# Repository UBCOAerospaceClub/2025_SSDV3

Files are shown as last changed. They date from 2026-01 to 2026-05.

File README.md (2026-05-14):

# The Super Step Down V3

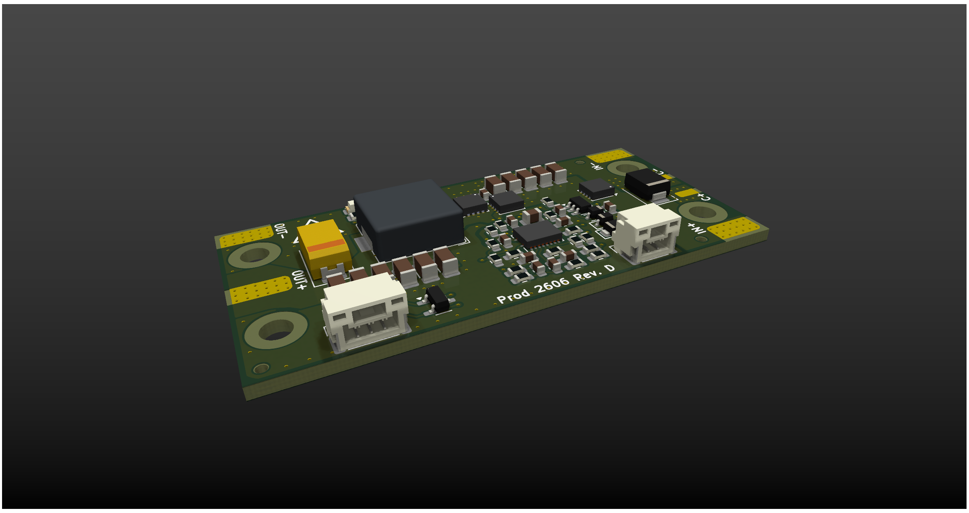
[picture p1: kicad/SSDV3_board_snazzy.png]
Top View


The SSDV3 is an independently-made, non-isolated DC/DC converter designed for unmanned aerial systems (UAS). The module is intended for converting 50V battery input down to 5-12V output at a maximum load of 8A. It acts as a reliable battery-eliminator circuit (BEC) through effective regulation in the presence of large line voltage and load current transients.

## Comparison with Last Super Step Down

This design is motivated by the challenges encountered by the [UBCO Aerospace Club](https://github.com/UBCOAerospaceClub) with their Jellyfish quadcopter when powering auxiliary electronics off the drone's main battery. Lessons were learned through a variety of integration failures, investigations, and verification, and these experiences informed the development of version 3 of the Super Step Down series.

Comparison

**Improvements from the previous version:**

- Dramatically improved regulation during line and load transients
- Considerable footprint area reduction by 16.5%
- Configurable output voltages instead of a fixed 5V output
- Added ESD protection on inputs
- Features reverse polarity protection
- Uses direct solder pads instead of terminal block for output connection

## Documentation

[Super Step Down V3 Documentation](https://docs.google.com/document/d/1HDTwUbcQu91JqGZ-epUO-CT9nVxvoZJ6mtjSmItczHE/edit?usp=sharing)

## Specifications

<table><tbody>
  <tr>
    <td>Input Voltage</td>
    <td>20-60V</td>
  </tr>
  <tr>
    <td>Max Transient Voltage</td>
    <td>100V (clamping starts at 70V)</td>
  </tr>
  <tr>
    <td>Output Voltage(s)</td>
    <td>5.1V, 7.4V, 12V</td>
  </tr>
  <tr>
    <td>Max Output Current*</td>
    <td>8A</td>
  </tr>
  <tr>
    <td>Typical Efficiency</td>
    <td>88%</td>
  </tr>
  <tr>
    <td>Voltage Transient Deviation</td>
    <td>±2.5%</td>
  </tr>
</tbody>
</table>

### Performance Curves

**Voltage ripple at 5.1V Output**

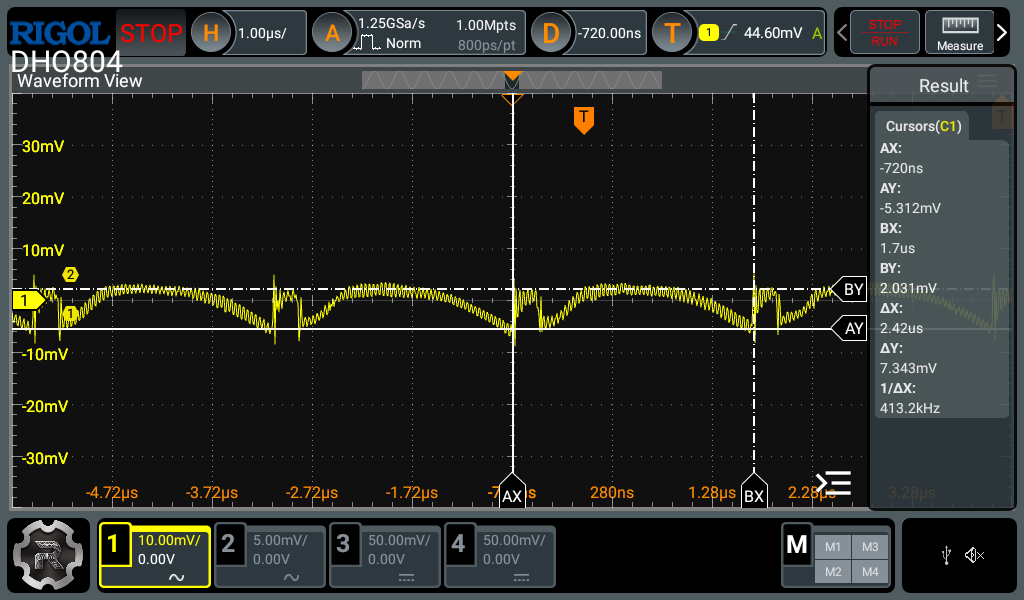
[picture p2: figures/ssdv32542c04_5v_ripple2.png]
Voltage ripple 5.1V


**Transient response of 5.1V 5-0A Output**

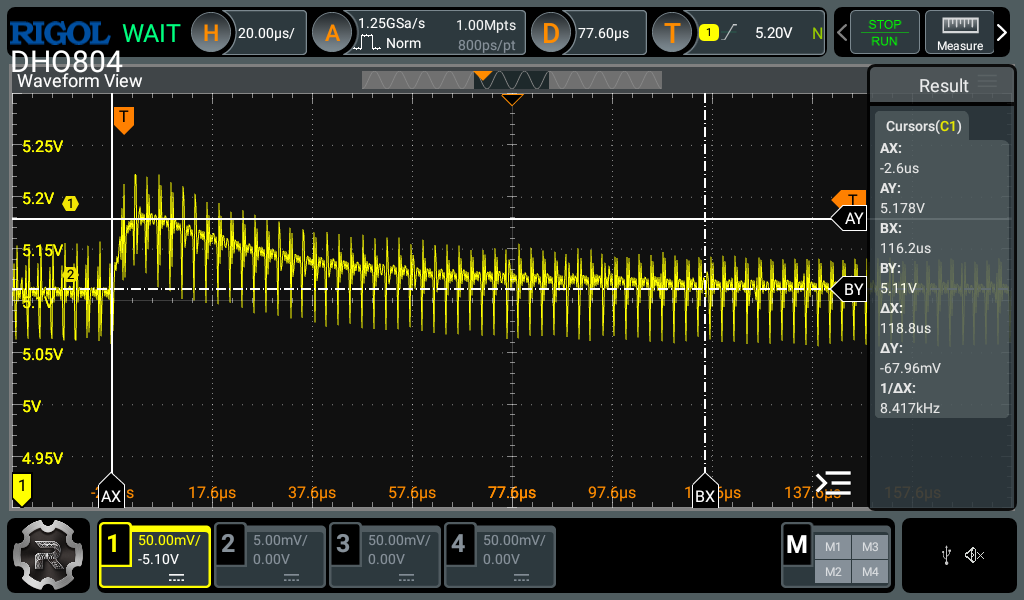
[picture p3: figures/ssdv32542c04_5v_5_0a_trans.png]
Transient response


**Efficiency Measurements, 50-V Input**

Efficiency curves

## Copyright Notice

Copyright &#169; Julian Joaquin 2026

Documentation and media are licensed under CC BY-SA 4.0

Hardware Source Licensed under CERN-OHL-W version 2

UBCO is registered trademark of the University of British Columbia. The use of UBC trademarks in this project are only for identification, and do not indicate association or endorsement. For guidelines on the permitted uses of UBC trademarks, please see http://universitycounsel.ubc.ca/university-trade-marks/.

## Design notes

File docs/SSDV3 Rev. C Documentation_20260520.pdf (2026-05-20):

### Super Step Down Documentation – SSDV3 Rev. C

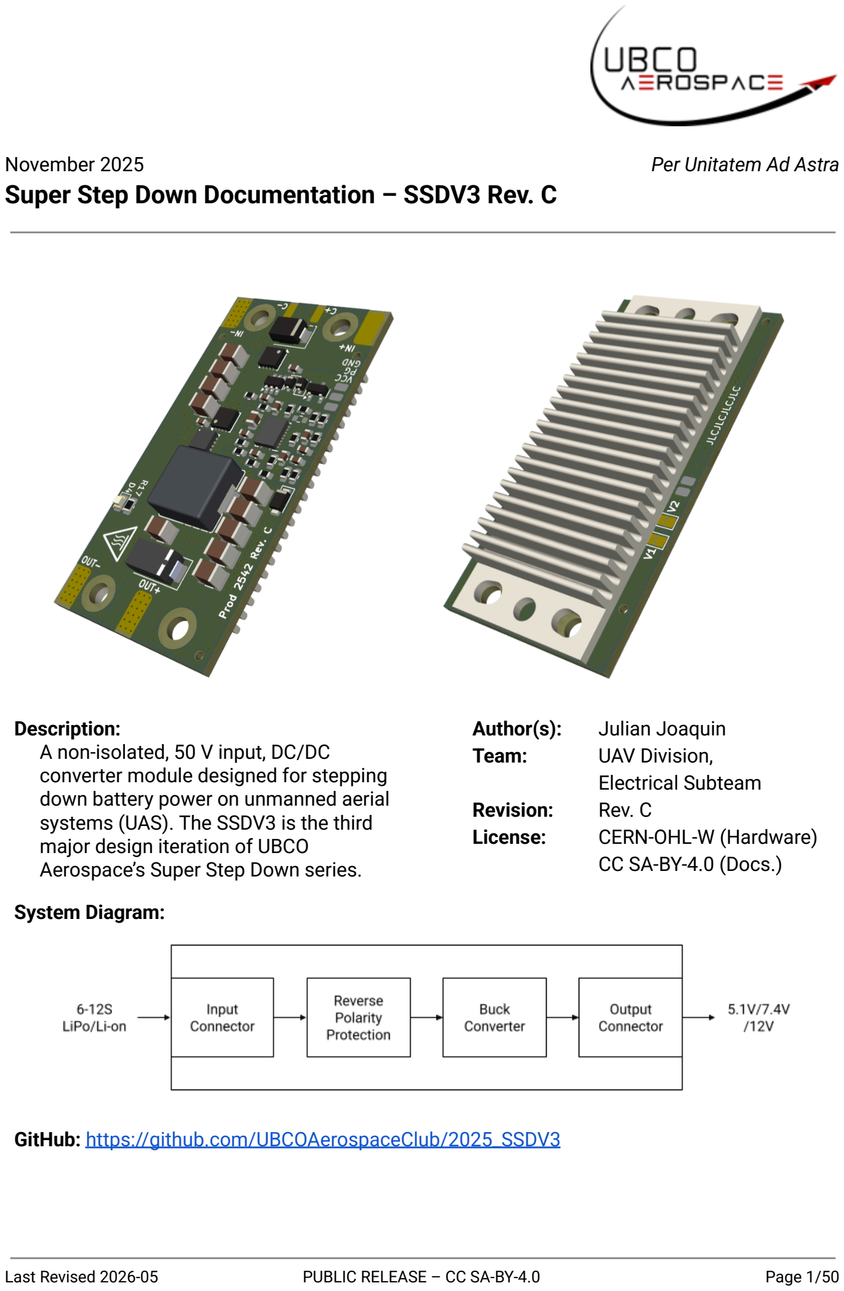
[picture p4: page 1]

November 2025 | Per Unitatem Ad Astra

Description:
A non-isolated, 50 V input, DC/DC converter module designed for stepping down battery power on unmanned aerial systems (UAS). The SSDV3 is the third major design iteration of UBCO Aerospace’s Super Step Down series.
Author(s): | Julian Joaquin
Team: | UAV Division,
| Electrical Subteam
Revision: | Rev. C
License: | CERN-OHL-W (Hardware)
| CC SA-BY-4.0 (Docs.)

System Diagram:

GitHub: https://github.com/UBCOAerospaceClub/2025_SSDV3

Last Revised 2026-05 | PUBLIC RELEASE – CC SA-BY-4.0 | Page 1/50

SSDV3 Rev. C Documentation

### Important Notice

The Complete Source material, including technical data, design resources, and other material associated with the SSDV3 project are provided “AS IS” without any guarantee of quality or compliance for commercial use.

UBCO Aerospace holds no rights to the patent of the SSDV3 project or its derivatives. The public documentation through UBCO Aerospace is solely provided for the purpose of compliance with CERN-OHL-W while it adopts the SSDV3 project for its own use.

UBCO is a registered trademark of the University of British Columbia. The use of UBC trademarks in this project are only for identification, and do not indicate association or endorsement from the university. For guidelines on the permitted uses of UBC trademarks, please see http://universitycounsel.ubc.ca/university-trade-marks/.

### Safety Precautions

Warning:
This device is intended to be directly connected to LiPo/Li-ion batteries which, under short-circuit conditions or unsafe handling, have the potential to cause fire or explosion. Take necessary precautions to insulate the device inputs and mitigate the risk of a short circuit.

Caution:
This device becomes hot under normal operation. Wait at least two minutes after powering off and allow the device to cool down to suitable temperatures before handling. When servicing, do not use low melting-point solder alloys, such as those that contain bismuth or indium.

Caution:
The input voltage to this device can be in excess of 60 VDC. Keep conductive materials away from the exposed device inputs. The device must be powered down before it can be handled or serviced.

Caution:
This device is susceptible to damage from electrostatic discharge (ESD). At minimum, refrain from touching any exposed copper or attached components to the PCB when handling without precautionary ESD measures.
Page 2/50 | PUBLIC RELEASE – CC SA-BY-4.0 | Last Revised 2026-05

### Design Revisions

Rev. | Date | Description
A-1 | 2025-07 | Concept design using the LM70880 buck converter and LM5069-1 hot-swap controller. Abandoned due to supply chain issues and cost constraints.
A-2 | 2025-08 | Concept design using the LM5146 buck controller and TPS2490 hot-swap controller. Abandoned due to space and cost constraints.
A-3 | 2025-09 | Concept design using the LM5146 buck controller in a custom 1/8th brick form factor. Accepted design for revision.
B | 2025-10 | Concept design using the cheapest parts available on LCSC. Limited part availability and NRND parts made future production of this revision difficult.
C | 2025-10 | Prototype design featuring reverse polarity protection in exchange for a smaller TVS diode on the input. Smaller, active-production 3x3mm PQFN-8 FETs used in place of SO-8 FETs. Used for preliminary integration testing and verification.
Last Revised 2026-05 | PUBLIC RELEASE – CC SA-BY-4.0 | Page 3/50

### Table of Contents

Page 4/50 | PUBLIC RELEASE – CC SA-BY-4.0 | Last Revised 2026-05

Last Revised 2026-05 | PUBLIC RELEASE – CC SA-BY-4.0 | Page 5/50

### 1 Specifications

### 1.1 Maximum Ratings

Under typical ambient temperature of TA = 21 °C, unless noted otherwise.
Parameter | Min Max | Unit
VIN | Input voltage from VIN+ to VIN- and C+ to C-1 | –60 60 | V
| Maximum transient input voltage 1 | –70 70
IIN | DC Input current | 6 | A
VEN | Input voltage from EN to GND 1 | –60 60 | V
VOUT | Output voltage from VOUT+ to VOUT- | 0 20 | V
IOUT | DC Output current | 8 | A
POUT | Output power for 60 seconds | 100 | W
| Continuous output power with heatsink | 60
| Continuous output power without heatsink | 40
VCC | Output voltage from VCC to GND | 0 7.8 | V
IVCC | Output current from VCC | 0.02 | A
VPG | Output voltage from PG to GND | 0 7.8 | V
TA | Operating ambient temperature range | 0 55 | °C
TSTG | Storage temperature range | 0 85 | °C
1. The input electrolytic capacitor is not protected from reverse polarity.
Page 6/50 | PUBLIC RELEASE – CC SA-BY-4.0 | Last Revised 2026-05

IMPORTANT:
Because of constrained budget, limited time availability, and project urgency, no SSDV3 Rev. C units have been used to verify the absolute maximum ratings. The provided ratings are estimated from available testing data and are not guaranteed to be the absolute maximum ratings before destruction of damage of the module.

### 1.2 Recommended Operating Conditions

Under typical ambient temperature of TA = 21 °C, unless noted otherwise.
Parameter | Min Max | Unit
S | Input LiPo/Li-ion cells in series | 6 12 | cells
VIN | Input voltage | 20 60 | V
| Maximum transient input voltage | 70
IOUT | VIN = 50 V, VOUT = 5.1 V, with heatsink 2 | 8.0 | A
| VIN = 50 V, VOUT = 7.4 V, with heatsink 2 | 5.8
| VIN = 50 V, VOUT = 12.0 V, with heatsink 2 | 4.0
| VIN = 25 V, VOUT = 5.1 V, with heatsink 2 | 8.0
| VIN = 25 V, VOUT = 7.4 V, with heatsink 2 | 8.0
| VIN = 25 V, VOUT = 12.0 V, with heatsink 2 | 6.6
2. Calculated from temperatures of load sweep test.

### 1.3 Electrical Characteristics

Under typical ambient temperature of TA = 21 °C, unless noted otherwise.
Parameter | Test Conditions | Min | Typ. | Max | Unit

### 1.3.1 Input Characteristics

VIN | Input voltage operating range | | 20 50 60 | V
IQ,ON | Quiescent input current, no load | VIN = 50 V, VOUT = 5.1V, no attached load to VOUT | 50 70 | mA
IQ,OFF | Quiescent input current, UVLO | VIN = 10 V | 2.7 | mA

### 1.3.2 Dynamic Characteristics

fSW | Switching frequency | | 417 | kHz
tSS | Soft-start time | VIN = 50 V | 3.6 | ms
IIN,MIN | Minimum startup supply current | VIN = 50 V, VOUT = 12.0 V | 0.6 | A
ΔVMAX | Maximum transient output deviation | VIN = 50 V, VOUT = 5.1V, 5 A load step | ±1.5 ±3.1 | %
Last Revised 2026-05 | PUBLIC RELEASE – CC SA-BY-4.0 | Page 7/50

### 1.3 Electrical Characteristics (continued)

Under typical ambient temperature of TA = 21 °C, unless noted otherwise.
Parameter | Test Conditions | Min | Typ. | Max | Unit

### 1.3.3 Output Characteristics

η | Efficiency | VIN = 50 V, VOUT = 5.1 V, IOUT = 4.3 A | 85 | %
| | VIN = 50 V, VOUT = 7.4 V, IOUT = 2.7 A | 87
| | VIN = 50 V, VOUT = 12.0 V, IOUT = 3.3 A | 91
ΔVPP | Peak-to-peak output voltage ripple | VIN = 50 V, VOUT = 5.1 V | 8.8 15.0 | mVPP
| | VIN = 50 V, VOUT = 7.4 V | 12.3 19.0
| | VIN = 50 V, VOUT = 12.0 V | 27.3 35.0
| | VIN = 25 V, VOUT = 5.1 V | 4.8
| | VIN = 25 V, VOUT = 7.4 V | 7.9
| | VIN = 25 V, VOUT = 12.0 V | 22.1

### 1.3.4 Protection Features

IOCP | OCP current limit threshold 3 | VIN = 50 V, VOUT = 5.1 V | 10.2 | A
| | VIN = 50 V, VOUT = 7.4 V | 10.5
| | VIN = 50 V, VOUT = 12.0 V | 11.6
OCP | Overcurrent protection | VIN = 50 V, VOUT = 5.1 V | PASS | : )
RPP | Reverse polarity protection | VIN = 50 V | FAIL 1 | : (

### 1.3.5 Auxiliary IO Characteristics

VEN,ON | Enable voltage | Input voltage rising | 16.3 | V
VEN,OFF | Undervoltage lockout threshold | Input voltage falling | 14.8 | V
VVCC | VCC nominal voltage | VIN = 50 V | 7.5 | V
VPG | PG nominal voltage | VIN = 50 V | 7.5 | V
1. The input electrolytic capacitor is not protected from reverse polarity.
3. Defined by design, not subject to testing.
Page 8/50 | PUBLIC RELEASE – CC SA-BY-4.0 | Last Revised 2026-05

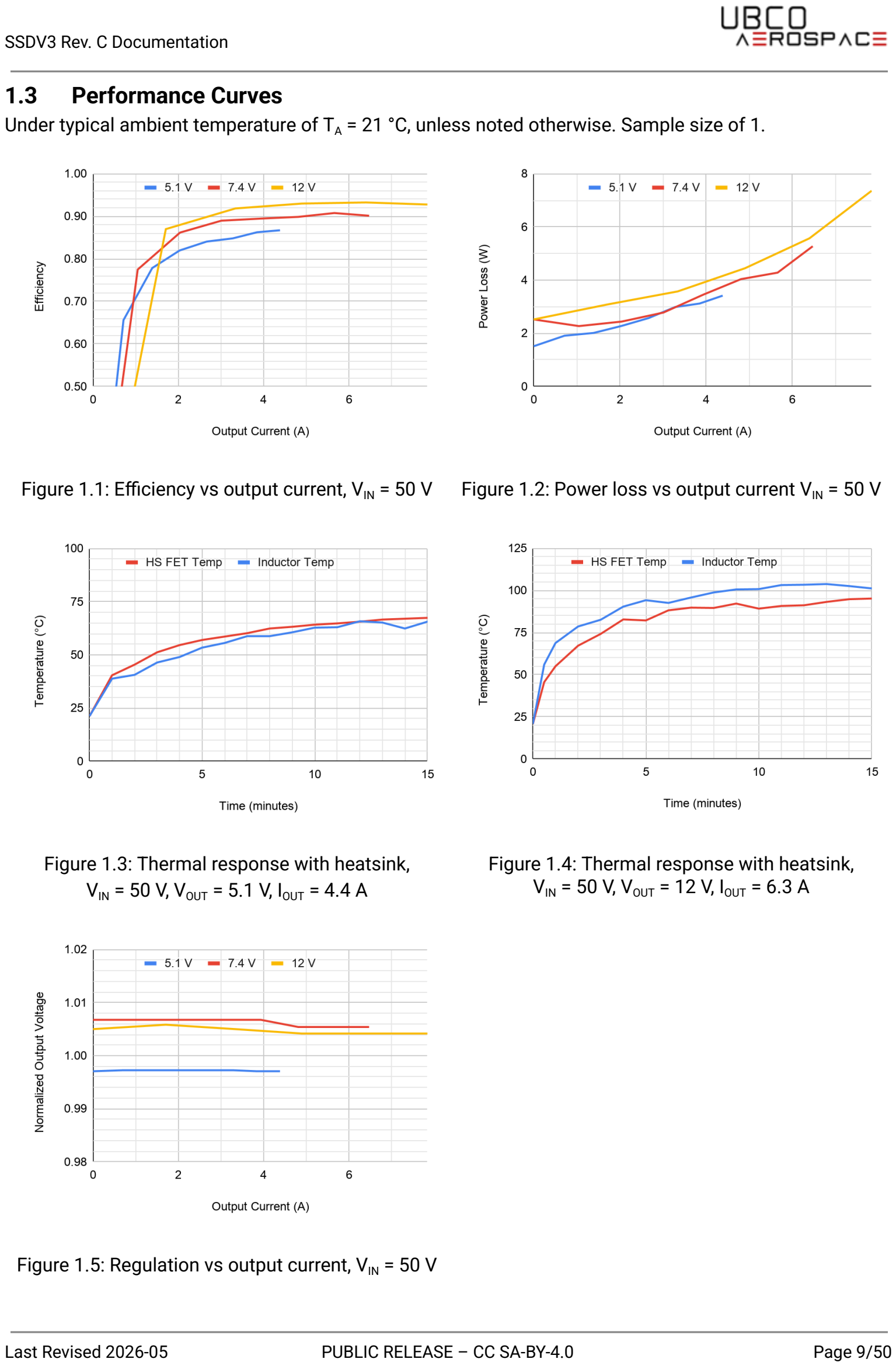
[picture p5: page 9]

### 1.3 Performance Curves

Under typical ambient temperature of TA = 21 °C, unless noted otherwise. Sample size of 1.

Figure 1.1: Efficiency vs output current, VIN = 50 V Figure 1.2: Power loss vs output current VIN = 50 V

Figure 1.3: Thermal response with heatsink, VIN = 50 V, VOUT = 5.1 V, IOUT = 4.4 A

Figure 1.4: Thermal response with heatsink, VIN = 50 V, VOUT = 12 V, IOUT = 6.3 A

Figure 1.5: Regulation vs output current, VIN = 50 V

Last Revised 2026-05 | PUBLIC RELEASE – CC SA-BY-4.0 | Page 9/50

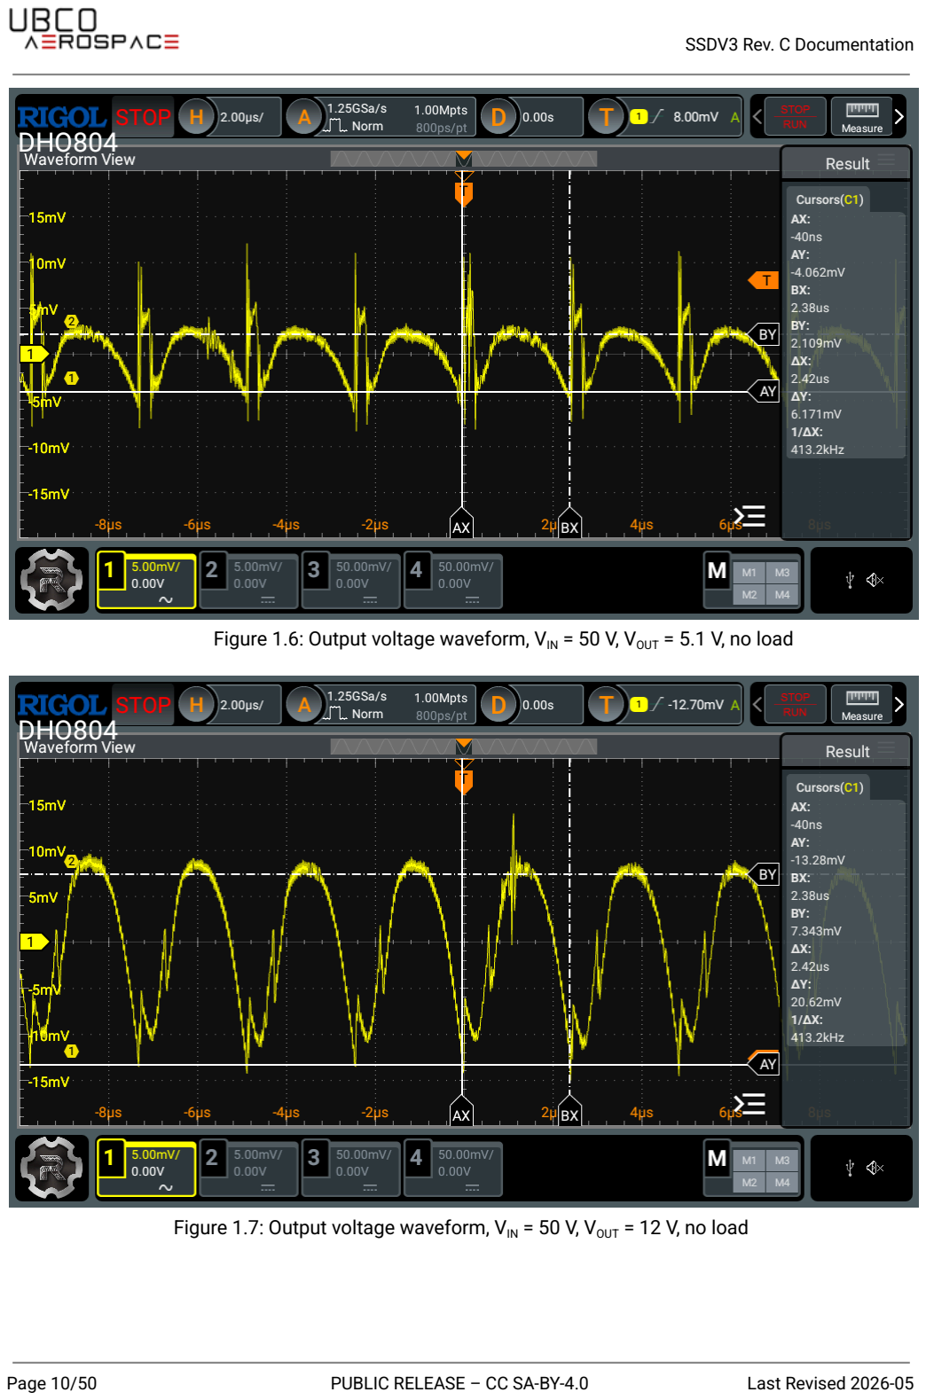
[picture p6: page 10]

Figure 1.6: Output voltage waveform, VIN = 50 V, VOUT = 5.1 V, no load

Figure 1.7: Output voltage waveform, VIN = 50 V, VOUT = 12 V, no load

Page 10/50 | PUBLIC RELEASE – CC SA-BY-4.0 | Last Revised 2026-05

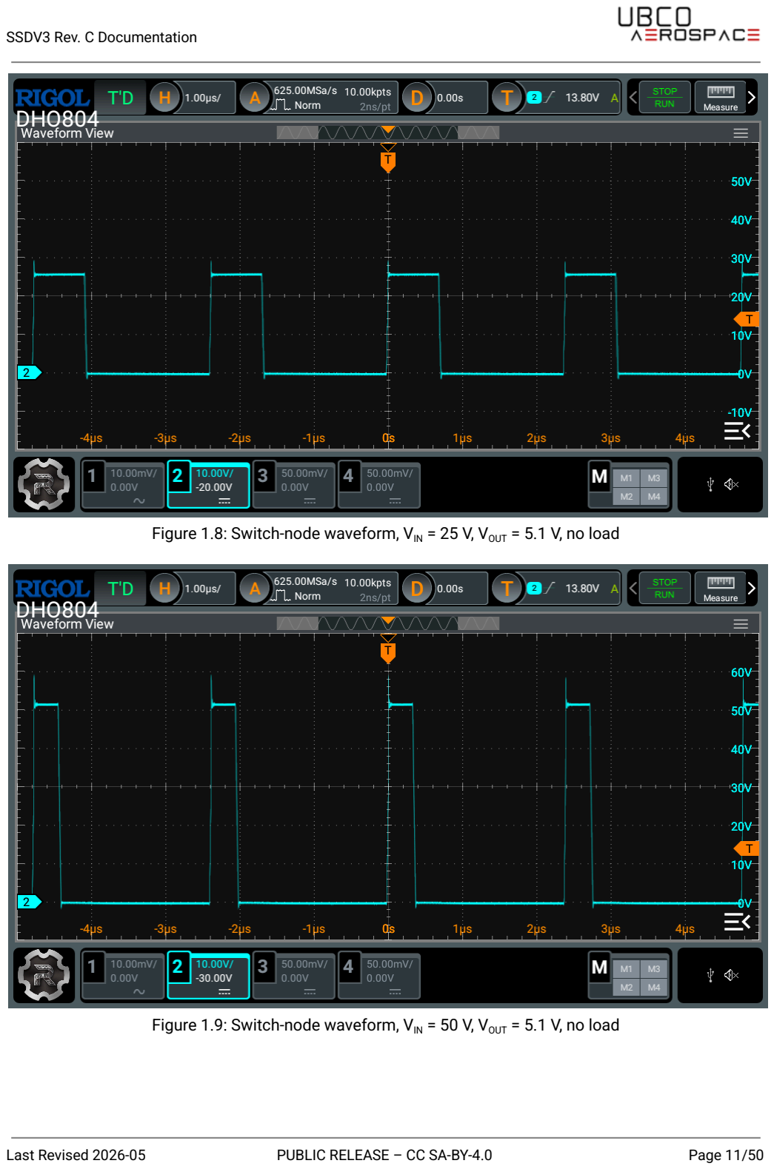
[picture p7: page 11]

Figure 1.8: Switch-node waveform, VIN = 25 V, VOUT = 5.1 V, no load

Figure 1.9: Switch-node waveform, VIN = 50 V, VOUT = 5.1 V, no load

Last Revised 2026-05 | PUBLIC RELEASE – CC SA-BY-4.0 | Page 11/50

Figure 1.10: Output load-on transient, VIN = 50 V, VOUT = 5.1 V, IOUT = 5 A

Figure 1.11: Output load-off transient, VIN = 50 V, VOUT = 5.1 V, IOUT = 5 A

Page 12/50 | PUBLIC RELEASE – CC SA-BY-4.0 | Last Revised 2026-05

### 2 Usage

Please read the Safety Precautions before continuing.

### 2.1 Functional Description

The SSDV3 is a non-isolated, wide input voltage step-down module intended to provide a reliable voltage source for electrically demanding systems requiring power from LiPo/Li-ion batteries. The design offers excellent disturbance rejection from battery voltage sag and sudden load spikes, giving much better performance than other hobbyist devices, making it a strong alternative to commercially-available battery eliminator circuits (BECs) while maintaining a small form-factor. Its extremely robust output regulation makes the SSDV3 best suited for supplying low-voltage devices, especially high-performance embedded computers or sensitive electronics that specify strict 5 V power requirements.

What makes the SSDV3 unique from other market BECs is its design for reliability. The step-down circuitry is protected by a TVS diode to address potential ESD on the battery lines. Copper traces leading from the input pads are designed significantly above specification to mitigate damage from inrush current whenever the battery is plugged in. Additionally, an N-channel MOSFET at the input acts as an ideal diode to protect the module and downstream electronics from a reversed battery connection, at minimal cost to the step-down’s efficiency.

### 2.2 Known Issues

Issue | Severity | Impact | Workaround | Planned Fix
Solder pads expose high-voltage contacts | High | Catastrophic battery short | Kapton tape covering | Board-mount connectors
Electrolytic cap. unprotected from reverse polarity | High | Reverse polarity will explode cap. | Do not reverse input | Reroute cap. to protected net
Thermal output limits current output below 8 A | Medium | Requires heatsink and thermal derating | Limit output | Lower losses
Output cap. placement causes large ESL spikes | Low | Output ripple spikes | None | Improve cap. layout

Table 2.1: Known issue risk assessment.

Last Revised 2026-05 | PUBLIC RELEASE – CC SA-BY-4.0 | Page 13/50

### 2.3 Interfaces

Figure 2.1: Module top interfaces.

Figure 2.2: Module bottom interfaces.

Page 14/50 | PUBLIC RELEASE – CC SA-BY-4.0 | Last Revised 2026-05

### 2.4 Installation Guidelines

- Ensure wires of at least 18 AWG have been soldered onto the input power and output power pads before installing the module. Use power connectors rated for the intended output current, for example the Amass XT30 or Molex Mini-Fit connectors.
- A heatsink must be installed for power outputs above 40 W (estimated). The screw hole arrangement is specifically designed to work with 1/8th brick DC/DC converter heatsinks like the Aavid 241802B92200G or Wakefield-Vette 567-45AB. An insulating thermal pad must be used between the heatsink and the PCB to prevent conduction through the soldermask. The recommended thermal pad for this module is the Berquist Gap Pad 1500 at 1 mm or 0.5 mm thickness, cut into a 20 mm × 40 mm rectangle.
- The module should be mounted to the vehicle or system chassis with four M3 screws and four M3 nylon standoffs. Use metallic fasteners at your own risk, as they may conduct from the exposed power input/output solder pads.
- To mitigate the risk of conduction from the power input pads on the edges of the module, you may surround the input-side of the module with kapton tape. Only use electrical tape as a protective layer on top of kapton tape for environmental resistance; electrical tape alone weakens with heat and will not completely prevent conduction to exterior materials.
- It is not recommended to surround the entire module and heatsink with an enclosure or heatshrink, as the design is intended to operate with natural convection cooling. Doing so will trap heat within the assembly and elevate the MOSFET junction temperatures above their maximum ratings.
- Wires introduce additional parasitics and can hamper the supplied voltage to the load. Parasitic resistance introduces a voltage drop across the wire, and becomes worse with greater current draw. Additionally, parasitic inductance in the wire creates much larger voltage drops during transient load events. To keep parasitics to a minimum, use the appropriate wire gauge for your intended maximum load, and keep the VOUT- and VOUT+ wires close together throughout their run to the load.
- The module is susceptible to damage when under vibration. Specifically, the large 1210 ceramic capacitors in the design may fracture with vibration, and may lead to a short-circuit. Take the necessary precautions to reduce the vibration experienced by the module, and always inspect for cracks in the capacitors before use.
- While the design features mitigation strategies to improve module resilience against inrush current, these strategies do nothing to actually prevent inrush current. It is recommended to have a separate system to address inrush current, such as pre-charging through an XT90S anti-spark connector, or through battery-side soft-start circuitry.
Last Revised 2026-05 | PUBLIC RELEASE – CC SA-BY-4.0 | Page 15/50

### 3 Motivation

In the past, the UBCO Aerospace UAV Division had used 6S LiPo battery packs for powering competition vehicles. The 25 V nominal output voltage allowed our electrical subteam to use the widely accessible LM2596 step-down module as “battery-eliminator circuits” (BECs) instead of using a secondary battery to power auxiliary electronics. The modules’ 42 V max input voltage, 3 A adjustable-voltage output, and very cheap availability eased the team’s development process and allowed us to spend less time working on power distribution and more time on addressing competition designs.

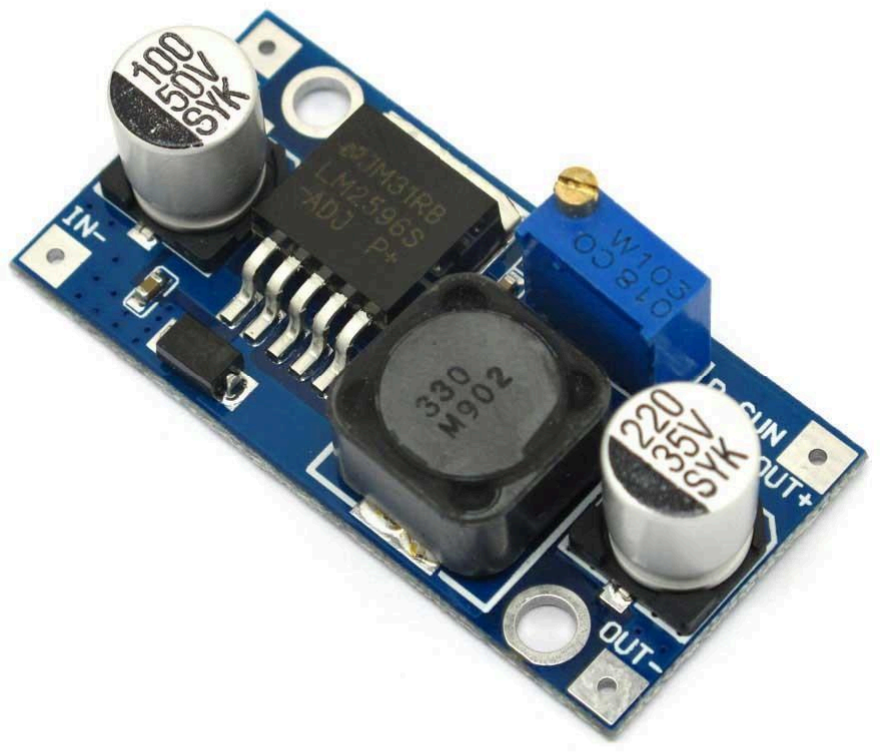
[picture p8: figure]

Figure 3.1: The trusty LM2596 module.

Since 2024, the UAV Division has migrated 12S (50 V) Li-ion battery systems for powering their competition vehicles. The higher voltage compared to previous 6S LiPo systems allows for the use of heavy-duty motors, improving vehicle thrust-to-weight ratios and payload capacity. This system comes with the tradeoff of requiring a brand new power architecture, since the 50 V operating voltage exceeds the LM2596’s ratings. Additionally, trends in the latest competitions have favoured partially or fully automated UAVs, and has led to the need for more powerful on-board computers that require more than the 3 A typically provided by LM2596 modules. These changes in the overall UAV system architecture are what motivate the design of a new step-down module for UBCO Aerospace.

### 3.1 Prior Solutions

Before the UAV division began using 12S battery packs for its drones, the club had already been using the HW-636 and HW-636B, a 60 V-rated, hobbyist step-down converter allegedly capable of providing up to 10 A output current. The primary motives for choosing the HW-636 were its small form-factor and low cost compared to other options. The electrical subteam encountered many issues with the HW-636, most notably catastrophic failures when adjusting the output voltage and destructive inrush current during battery connection. Integration tests also revealed poor voltage regulation once the output current exceeded 3 A, causing brownouts with our Raspberry Pi 5 onboard computer.

Page 16/50 | PUBLIC RELEASE – CC SA-BY-4.0 | Last Revised 2026-05

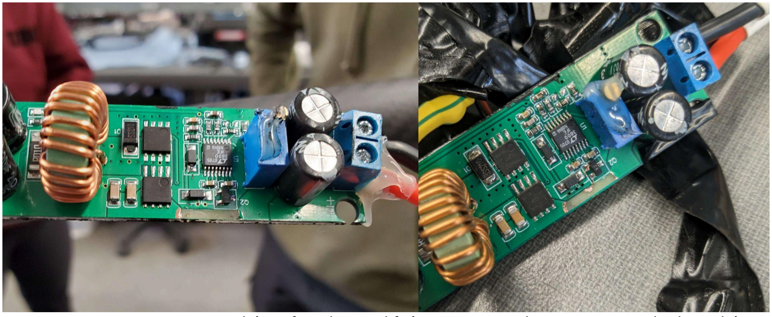
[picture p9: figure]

Figure 3.2: Two HW-636 modules after observed failures in 2025. The input trace on both modules exploded immediately after plugging in our 12S batteries.

Reliability issues motivated the team to design a custom solution using the Vishay SiC461 buck converter IC (which, contrary to the name, does not contain silicon carbide FETs), dubbed the Super Step Down V2 (or SSDV2). The converter would provide a 5 V bus to power servos and a Raspberry Pi 5. In spite of our efforts, testing revealed severe output ripple and poor regulation, with voltage deviations of up to ±10% and ripple voltage of 560 mVPP even with no load. During system integration, the output varied between approximately 4.8 V and 5.3 V, repeatedly causing brownouts at the Raspberry Pi and rendering the design unsuitable for powering our avionics. The fixed output prevented the team from adapting the design for other loads.

Root cause analysis identified insufficient output capacitance as the primary failure mechanism. A misinterpretation of the Vishay PowerCAD reference design led to the omission of twelve out of thirteen specified output capacitors, leaving the converter with much less than the required capacitance and severely degrading both transient performance and voltage regulation.

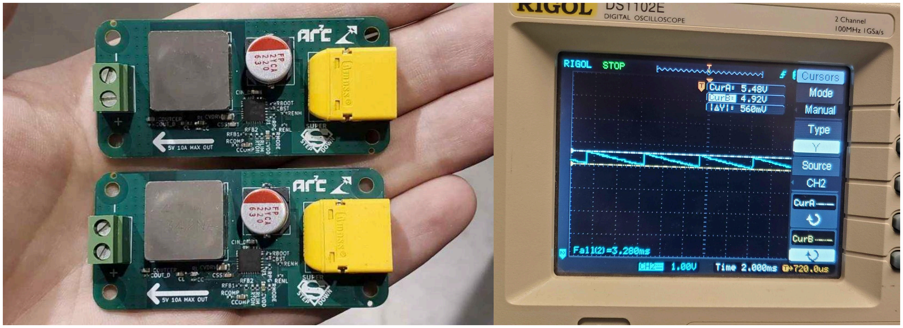
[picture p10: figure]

Figure 3.3: The SSDV2 fully assembled. Its design forgot to include output capacitors.

Last Revised 2026-05 | PUBLIC RELEASE – CC SA-BY-4.0 | Page 17/50

### 4 Circuit Design

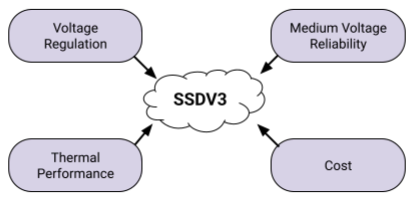
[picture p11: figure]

Figure 4.1: Major design factors of the SSDV3.

The main goal of the SSDV3 is to provide a well-regulated voltage under any condition, thus emphasizing the importance of designing for transient performance. Pure no-load measurements have not been an effective metric for testing our step-down modules. Our prior failures with both the HW-636 and the SSDV2 underline transient performance as the most critical design factor of the converter.

This design must also be resilient against inrush currents given the medium operating voltage. Our experience with the failures of the HW-636 show that ceramic capacitors on the input can easily result in inrush currents over 100 A upon sudden connection of a 50 V source, and that the precharge functionality of anti-spark XT90s cannot be relied upon to dampen such currents. As a result, the SSDV3 must be able to handle these inrush currents either through input damping or large copper pours.

While efficiency is not considered the top priority for this design, thermal shutdown or runaway could be a catastrophic failure mode if not accounted for. Our team previously did not make any considerations for thermal performance, other than noting the SSDV2 was very hot to touch during operation. Recent testing at 50 V input showed the MOSFET packages on the HW-636 reached 100 °C within 3 minutes when outputting 12 V at just 3 A, with the junction temperatures estimated to be operating close to 115 °C. The converter must be cooled solely through natural convection since our aircraft are usually designed with no chassis airflow.

Cost must be considered through the design, since funding across UBCO Aerospace has been spread thin for 2025-26. The component selection and board requirements must be carefully balanced with the overall unit cost in order for the production of the SSDV3 to be attractive over other commercial off-the-shelf solutions (COTS). This means restricting PCB specs to 4-layer, 1 oz copper, and taking advantage of “economic” processes from board manufacturers.

Finally, the solution footprint is a moderate factor influencing the SSDV3 design. Just as with cost, the size of the design must be competitive to other COTSs and the prior SSDV2.

Page 18/50 | PUBLIC RELEASE – CC SA-BY-4.0 | Last Revised 2026-05

### 4.1 Requirements

ID | Requirement Statement | Rationale
R-1 | The SSDV3 shall accept 6S and 12S battery input. | Typical for UAVs.
R-2 | The SSDV3 shall provide selectable regulated voltage outputs of 5.1 V, 7.4 V, and 12 V. | Supports common voltages for avionics and affectors.
R-3 | The SSDV3 shall provide a nominal output current of 5 A and a maximum output current of 8 A. | Power requirements for Raspberry Pi 5 plus margin.
R-4 | The SSDV3 shall maintain its regulated voltage with no more than 5% deviation. | Prevent downstream electronics brownouts.
R-5 | The SSDV3 shall limit its MOSFET junction temperature rise to no more than 80 °C. | Prevent thermal runaway or shutdown.
R-6 | The SSDV3 shall survive typical 50 V hot-plug events for UAV applications. | Based on HW-636 failures.
R-7 | The SSDV3 shall protect downstream electronics from short-circuit faults. | Improve UAV fault tolerance.
R-8 | The SSDV3 shall be no larger than the SSDV2. | Maintain a similar mechanical footprint for mounting.

Table 4.1: Key functional requirements for the SSDV3.

### 4.2 Converter Topology

The most suitable and simplest DC/DC converter topology for this design is the buck converter. More sophisticated topologies like the flyback or forward converter would not offer any benefit at the required power output, and the use of a transformer would only complicate the design. The solution space for buck converters at this power output can be broken down into three major categories:

- a buck converter IC with integrated FETs,
- a buck controller with external FETs, and
- a dual-phase buck converter

A buck converter IC represents the simplest option of the three, removing the challenge of choosing discrete MOSFETs and allowing for the smallest footprint. While a number of these buck converters are rated for 8-10 A output, their efficiency curves suggest total system power losses of 3-5 W, very likely requiring heatsinks in order to operate at these currents for prolonged periods. Granted, the losses from parasitics in an integrated buck converter will be lower than a converter with external FETs [1], but attempting to improve such high thermal dissipation in a single package will be challenging. The most promising IC at this time is the LM70880 buck converter from Texas Instruments (TI), optimized for high step-down-ratios, though also the most expensive option at $11.10 CAD per unit from DigiKey. Other solutions like

Last Revised 2026-05 | PUBLIC RELEASE – CC SA-BY-4.0 | Page 19/50

the MIC28516, LM76005, or SiC461 either are too inefficient at rated current, offer little voltage margin at VIN = 50 V, or use a variable-frequency control scheme that is not easy to design around.

Designing a buck converter using a controller and external FETs provides a greater amount of flexibility in the design, particularly in optimizing for either switching or conduction losses. Using discrete FETs also offers the benefit of greater heat spreading across the PCB, but comes with the cost of a more laborious PCB layout and necessitating more design time for selecting FETs. The selection of buck controllers is only limited by the 70 V max input voltage and minimum on-time specification of at least tON ≈ 5 V / 70 V / 500 kHz = 140 ns [2]. Once again from TI, the LM5146 and LM5148 buck controllers appear to be the most attractive options, at $2.49 and $2.25 CAD on LCSC respectively. With most 100 V MOSFETs costing about $1.50 CAD each, we could potentially design a discrete-FET synchronous buck converter for nearly half the cost of the LM70880! The cost alone makes a discrete-FET buck converter the most attractive approach.

Using a dual-phase buck converter reduces both the ripple voltage and transient deviation of a typical buck converter. In fact, modern motherboard voltage regulator modules (VRMs) are implemented as multi-phase buck converters that are specifically optimized for fast transient CPU loads, suggesting that a similar approach is well-suited for supplying embedded computers like the Raspberry Pi 5. Two phases also hypothetically reduces the solution size, since two small inductors are typically smaller than one large inductor [3]. The compromise of this approach is it requires twice as many FETs compared to a single phase converter, and possibly two controllers as well. A number of dual-phase buck reference designs exist from TI for both the LM5148 and LM5143 controllers. While these designs show that a multi-phase buck converter can reduce the number of passive components, the overall solution size is typically larger than that of a single-phase buck converter and provides substantially more power than required for this application.

Evidently a buck controller with external FETs was chosen for the topology of this design.

Page 20/50 | PUBLIC RELEASE – CC SA-BY-4.0 | Last Revised 2026-05

### 4.3 PWM Control Method

At a glance, both the LM5146 [4] and LM5148 [5] equally meet the design requirements set out in 4.1. Choosing between the two ICs comes down to deciding whether the buck converter PWM generation should use voltage-mode control (VMC) with line feed-forward or current-mode control (CMC). This decision must be made early in the design process to determine the desired inductor current ripple factor.

An abhorrent amount of my time has been spent researching the most optimal control mode, with what felt like hundreds of research papers, conference papers, and application notes. The most useful resources were [6-13] for making this decision. In general:

- Current-mode control simplifies the plant by changing the output stage LC double pole to a single RC pole. This is desirable for topologies with right-half-plane-zeros (not the buck converter.)
- Both VMC and CMC can provide good line rejection. In spite of praise for CMC’s “intrinsic feed-forward” sensing via inductor current for line variations, VMC with feed-forward is still encouraged for applications with large line transients without much justification.
- Voltage-mode requires more compensation circuitry compared to current mode.
- Current-mode control requires current sensing which can be susceptible to interference. Sensing may also require blanking time to eliminate leading-edge current spike, increasing high-side switch minimum on-time (though there is no mention of blanking time in the LM5148 datasheet).
- Current-mode control may suffer from subharmonic oscillations for duty cycles above 50% (which isn’t very applicable to this design.)
- The LM5148 requires the inductor to be specified to match the appropriate inductor current ripple downslope for its internal slope compensation, with the ideal inductor calculated using Equation 9 from the datasheet [9]. This specification can conflict with the rule-of-thumb inductor current ripple factor of 0.2-0.4.

The tradeoffs between the two control techniques can be discussed endlessly and is not the subject of this section.

The deciding factor for choosing the controller was the ease of understanding the small-signal transfer function of each control technique. The described voltage-mode analysis in [14-16] was easier for me to understand and implement compared to the current-mode analysis in [17] and [18]; additional design parameters for slope compensation and modulator gain made derivation of the control-to-output transfer function unclear to me at the time. Hence the LM5146 was selected.

Last Revised 2026-05 | PUBLIC RELEASE – CC SA-BY-4.0 | Page 21/50

### 4.4 Power Stage

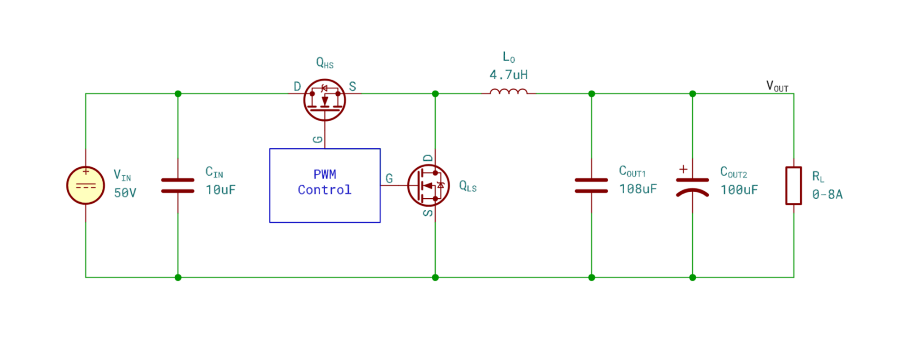
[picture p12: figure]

Figure 4.2: The SSDV3 simplified power stage.

The power stage of the buck converter consists of the input capacitors, the high-side and low-side switching MOSFETs, the inductor, and the output capacitors. The component values were selected sequentially, beginning with switching frequency and desired inductor ripple factor, then the MOSFETs, followed by output capacitance sizing based on output ripple and transient constraints, and finishing with input capacitance selection for input ripple and bulk energy considerations.

The calculations for the power stage components used equations from [19] and [20], alongside assistance from the LM5146/-Q1 quickstart design tool available from TI.

Page 22/50 | PUBLIC RELEASE – CC SA-BY-4.0 | Last Revised 2026-05

### 4.4.1 Switching Frequency and Inductor Selection

One of the critical design parameters of a buck converter is the inductor current ripple, which is usually expressed as a ratio to the maximum output current, and it can only be controlled through the choice of inductor and switching frequency. A large current ripple causes higher power loss in the inductor through hysteresis loss and increased output voltage ripple, while a ripple that is too small requires a very big inductor and hampers voltage regulation due to limited current slew rate (illustrated in Figure 9-1 of the LM5146 datasheet [4]). A current ripple of 30% is widely used as a rule-of-thumb for buck converters and is set out as the desired ripple for this design.

Inductor current ripple is strongly dependent on the converter duty ratio, which will vary for the different output voltages of 5.1 V, 7.4 V, and 12 V. Since it will not be possible to optimize the current ripple for all three output voltages with voltage-mode control, a compromise is made, and a 30% current ripple is only designed for the 5.1 V output voltage since it is expected to power the most sensitive equipment. This compromise results in the 12 V output mode having a ripple current of about 50%, trading the benefit of higher current slew rate not hindering transient performance with increased power loss and greater output voltage ripple.

Since this design is intended to be assembled abroad, the choice of components must be optimized for availability with Eastern distributors like LCSC. A quick search for parts from well-known manufacturers on LCSC show that only E3 series inductors are usually well stocked. Knowing that the required switching frequency range is limited by the effects of switching power loss, and that larger inductors are also bulklier and carry higher resistance, a 4.7 μH inductor is chosen as the optimal balance between all factors. Consequently, the switching frequency is specified to 420 kHz to achieve a 30% current ripple at VOUT = 5.1 V.

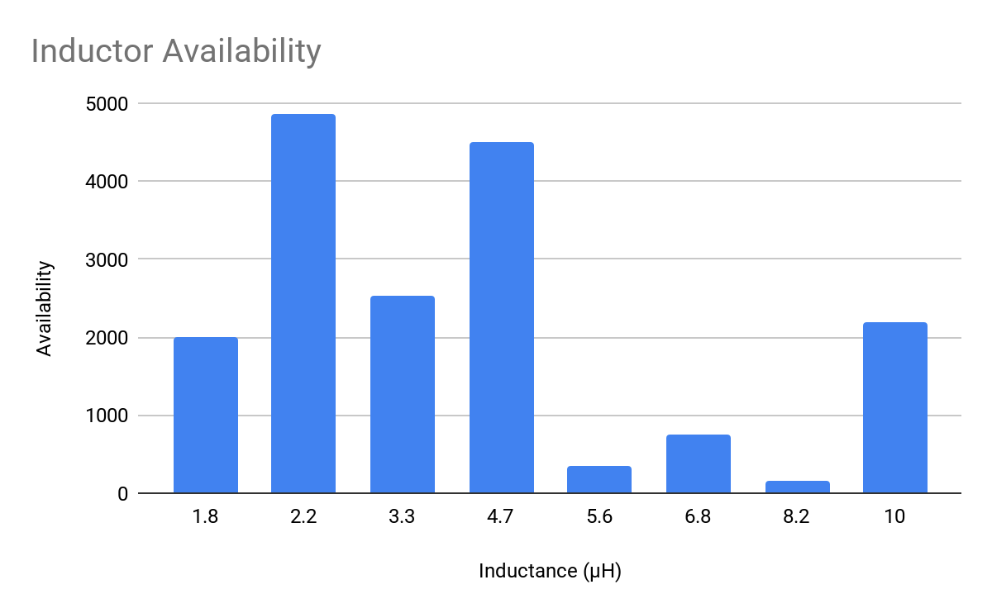
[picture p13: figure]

Figure 4.3: The availability of different inductor sizes on LCSC that meet the design specifications.

Last Revised 2026-05 | PUBLIC RELEASE – CC SA-BY-4.0 | Page 23/50

### 4.4.2 MOSFET Selection

Typical textbook literature about MOSFETs in switching applications describe two sources of power loss: RDS(on)

losses when the MOSFET is on, and QG losses in turning the MOSFET on or off. Guidance from [21], [22], and the equations 10-12 in [23] reveal a “third” source; Qoss + Qrr transition losses between the low-side MOSFET parasitics (also called the synchronous rectifier) and high-side MOSFET turn-on event can easily dominate over the other losses at the intended 50 V input voltage, since they are directly proportional to the input voltage:

PHS turn-on ≈ (Qoss + Qrr)LS × VIN × fSW (back-of-the-envelope estimate).

Further complicating things, both [22] and [24] explain that the Qoss and Qrr datasheet specifications are strongly dependent on the exact MOSFET drivers, and that the test conditions in the datasheet seldom align with real world switching applications, even if the test voltage matches the intended operating voltage. Unfortunately UBCO Aerospace does not have the necessary test equipment to independently verify the Qoss and Qrr parameters of each MOSFET candidate, so the datasheet specifications will have to be taken at face value for comparisons.

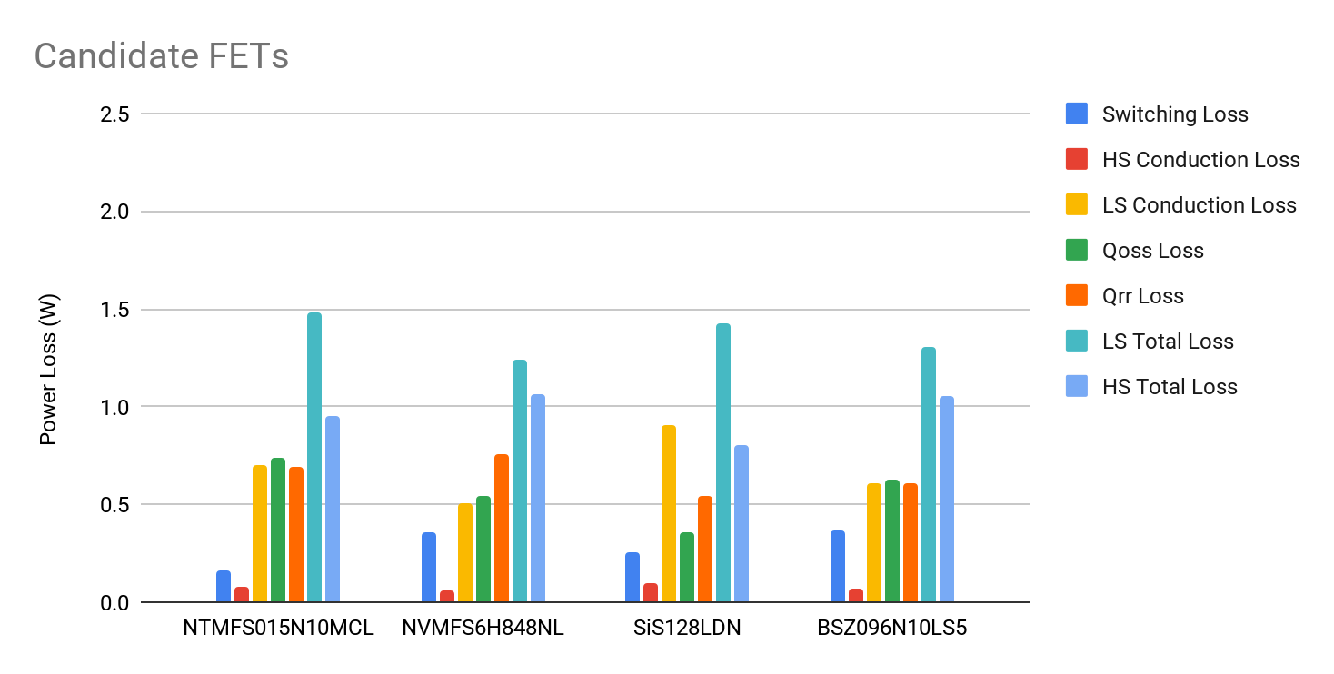
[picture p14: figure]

Figure 4.4: Power loss breakdown of some candidate MOSFETs.

The figure above analyzes the power losses of some of the best candidate parts that were available on LCSC for Rev. C, using the methodology described in [23]. The BSZ096N10LS5 [25] from Infineon was chosen as the low-side MOSFET for its high availability and equal losses across each category compared to the other options. However, the relatively high singular unit cost of $1.93 CAD through LCSC motivated choosing a different part for the high-side MOSFET. With a simpler (RDS(on) × QG) figure-of-merit, the CSD19537Q3 [26] from TI was chosen for the high-side MOSFET with a very competitive $1.12 CAD singular unit cost.

Significant BVDSS derating of 60-100% from the nominal operating voltage of 50 V was chosen to account for UAV motor regenerative back EMF and TVS diode clamping voltage variation [27].

Page 24/50 | PUBLIC RELEASE – CC SA-BY-4.0 | Last Revised 2026-05

### 4.4.3 Capacitor Selection

The selection of output capacitors is one of the more nuanced elements of the design process for this project. The output capacitors are the defining factor for output ripple and transient performance, and also impact the later controller implementation through their contribution of a pole-zero pair to the power stage transfer function [28]. Generally more capacitance with a low ESR improves all quantitative factors of a buck converter in exchange for greater production costs and board space.

This design takes a hybrid approach and uses a combination of ceramic and polymer tantalum capacitors to simultaneously address both voltage ripple and transient performance, achieving both low ESR and high energy density in a small form-factor. This approach takes inspiration from the consumer graphics cards, where power filtering uses a combination of ceramic and tantalum capacitors to meet the strict voltage requirements of GPU chips [29]. The drawback of using two different capacitor chemistries is it complicates the power stage transfer function by adding another pole and zero to the system [30]. To keep the design simple, the value of the ceramic capacitors is roughly matched to the size of the tantalum polymer capacitor, resulting in the added pole and zero to roughly cancel out.

The output capacitance is realized using one KEMET T521D107M025ATE040 100 μF KO-CAP tantalum capacitor, and six Samsung CL32A226KAJNNNE 22 μF X5R ceramic capacitors, with an effective capacitance of 108 μF at 5 V and 53 μF at 12 V. A polymer tantalum capacitor was chosen over a polymer electrolytic capacitor to keep the module size compact.

The input capacitors are important for minimizing input ripple and switch-node parasitics. In this application only ceramic capacitors are used at the input for their low ESL and small footprint, minimizing the design's parasitic loop inductance. Four Murata GRM32EC72A106KE05 10 μF, 100 V rated ceramic capacitors implement the input capacitance, with total effective capacitance of 10 μF at 50 V. An additional 100 nF 0603 capacitor is used to keep the switching current loop tight near the power stage MOSFETs and minimize loop inductance.

An additional 47 μF electrolytic capacitor is added to the input only for the purpose of damping wire resonances.

Last Revised 2026-05 | PUBLIC RELEASE – CC SA-BY-4.0 | Page 25/50

### 4.5 Controller Implementation

### 4.5.1 IC Power Input

The power input to the LM5146 buck controller uses a 2.2 Ω series resistor with a 100 nF decoupling capacitor to provide minor high frequency filtering from the 50 V input line.

### 4.5.2 UVLO Implementation

Accounting for converter dropout voltage, the UVLO is set to 15 V, or about 3 V above the maximum output voltage of 12 V.

### 4.5.3 Soft Start

The anticipated operating conditions of the converter does not involve highly capacitive loads, so a modest 4 ms soft-start period is implemented through a 47 nF capacitor on the SS pin.

### 4.5.4 Bootstrap Circuit

The high-side gate driver uses a bootstrap circuit to keep the high-side MOSFET on by allowing the gate voltage to momentarily swing above VIN for the duration of the switching on-time [31].

The chosen high-side MOSFET does not present a demanding switching action under regular operation to the LM5146’s internal gate driver circuitry, so a typical 100 nF capacitor is sufficient. A 2.2 Ω series resistor is also used to slow down the turn-on time of the high-side MOSFET and consequently reduce switch-node ringing [32].

### 4.5.5 OCP Implementation

The OCP threshold was arbitrarily defined as roughly 50% of the maximum drain current of both MOSFETs at 125 °C, specified by their datasheets. The threshold is hence constrained by the CSD19537Q3 with a max ID ≈ 23 A at 125 °C [26], so the OCP target threshold is set to 11.5 A.

The OCP is implemented using the low-side MOSFET Rds(on) sensing method defined in the LM5146 datasheet. The RILIM resistor is set to 430 Ω, an E24 series value, alongside a 12 pF C0G decoupling capacitor to address the 6 ns RC time constant requirement from the datasheet.

### 4.5.6 FPWM/DEM Mode

With the objective of excellent transient performance under all conditions, FPWM mode is set for light-loads. This is implemented using a 20 kΩ pull-up resistor on the SYNCIN pin to the IC VCC rail. In the event that DEM mode is desirable, a 0 Ω resistor can be placed on the DNP’ed R8 to pull the SYNCIN pin to GND.

Page 26/50 | PUBLIC RELEASE – CC SA-BY-4.0 | Last Revised 2026-05

### 4.6 Feedback and Loop Compensation

Voltage-mode buck converters require a type-III compensator to achieve closed-loop stability [33], shown in Figure 4.5. An integrator pole and a pole-zero pair are introduced through the compensator feedback impedance on the op amp, internal to the LM5146. A second pole-zero pair is added through the input impedance to the op amp inverting input.

Compensation is conventionally achieved through loop shaping–placing the compensator zeroes near the power stage resonance frequency, a compensator pole near the power stage output capacitor ESR zero, and another pole at fSW / 2 to achieve
the desired gain and phase margin [14].

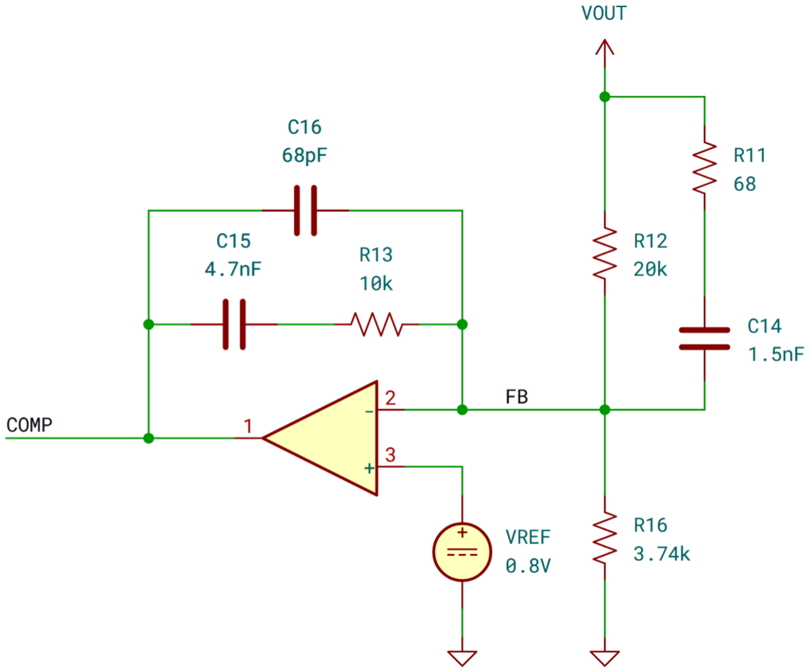
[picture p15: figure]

Figure 4.5: The type-III compensator circuit.

The TI-provided LM5146/-Q1 quickstart design tool includes fields for automatically designing the compensator, but the tool is only intended for a single type of output capacitor. Hypothetically this should be fine for this mixed output capacitor design, since the different output capacitors were specifically selected so the introduced poles and zeroes would remain simple. But DC bias effects on the ceramic capacitors meant the power stage output double-pole would migrate in frequency with different output voltages (e.g. 7.4 V and 12 V).

The compensation‑tuning method had become somewhat crude. To preserve the convenience of the quickstart design tool, the control‑to‑output transfer function was first derived in Figure 4.6 and used in MATLAB for the various output capacitors. An equivalent single‑capacitor model was then estimated by inspecting the bode plot and pole‑zero locations, and the resulting ESR and capacitance were entered back into the tool. The tool’s compensator parameters were finally re‑checked in MATLAB to verify open‑loop behavior and stability margins. This process produced a compensator with robust stability across all output voltages.

Figure 4.6: Derivation of the control-to-output transfer function using the state-space averaged buck converter model and generalized capacitors. Input voltage and output current perturbations are zeroed.

Last Revised 2026-05 | PUBLIC RELEASE – CC SA-BY-4.0 | Page 27/50

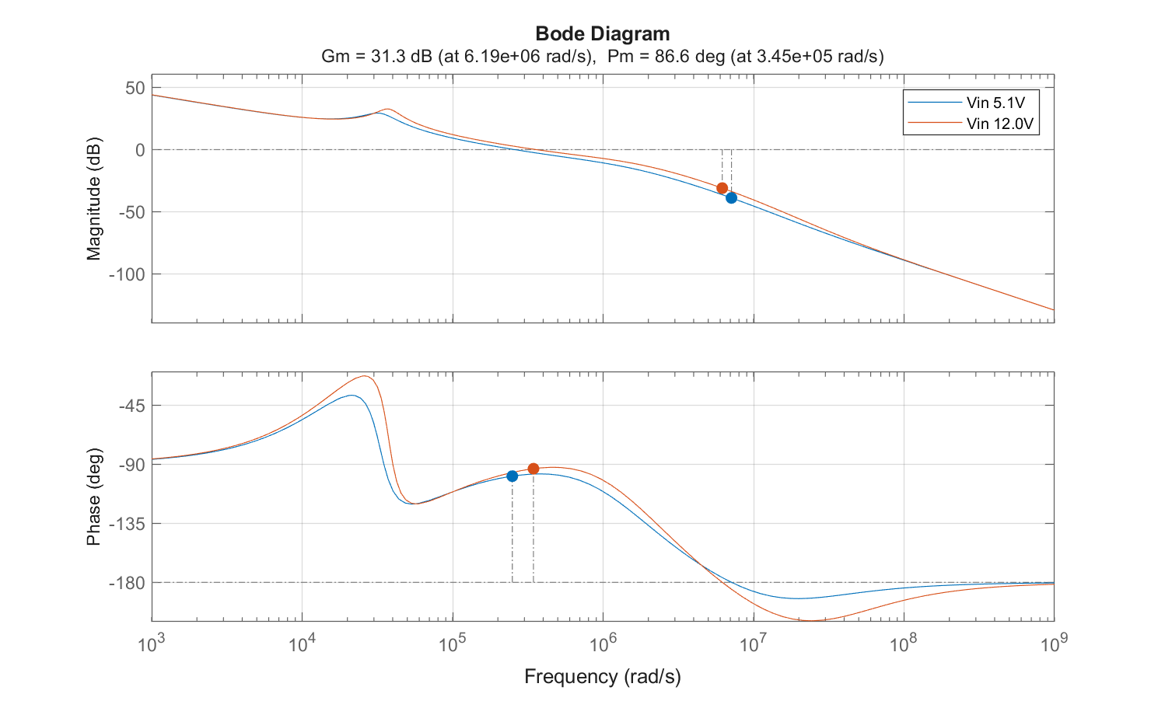
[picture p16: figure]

Figure 4.7: The full open-loop transfer function bode plot, after compensation.

Figure 4.7 illustrates the bode-plot and stability margins of the open-loop system with compensation. The 5.1 V output has a phase margin of 80.9° at a crossover frequency of 39.6 kHz. The 12 V output has a phase margin of 86.6° at 54.9 kHz. While the stability margins seem extreme, well above the 60° phase margin typical for robust control, the migrating double-output pole caused by the DC bias effect on the output capacitors made it difficult to balance the phase with the target crossover frequency of fSW / 10 through compensation. The aggressive margins are simply the result of attempting to balance the control bandwidth with loop stability.

Though unmentioned in the motivation section of the documentation, UBCO Aerospace encountered one noted issue with the SSDV2 where the output voltage seemed to drift over time as the module provided power to a demanding load. It is hypothesized the voltage drift was caused by the changing of value on the thick-film feedback resistors from temperature drift as the SSDV2 heated up [34]. To prevent this issue from surfacing again in the SSDV3, the lower resistors on the feedback voltage divider use thin-film resistors with very low temperature coefficients of 50 ppm/°C or lower. This is why the voltage-setting resistors use E96 series resistors, while every other resistor is from the E24 series.

On a smaller note, the user sets the desired output voltage by shorting jumper pads that “enable” the lower resistors in the voltage divider. If each target voltage of 5.1 V, 7.4 V, and 12 V had its own dedicated lower resistor, a user could accidentally short both the 7.4 V and 12 V jumpers, producing a much higher output voltage than intended. To prevent this, the lower resistors are chosen so that achieving 12 V requires shorting both jumpers. The different output voltage configurations based on the shorted jumpers is shown on the silkscreen of Figure 2.2.

Page 28/50 | PUBLIC RELEASE – CC SA-BY-4.0 | Last Revised 2026-05

### 4.7 Reverse Polarity Protection

The initial design schematics had circuitry for input hot-swap protection, rather than reverse polarity protection, since we had assessed inrush current to be a major risk. However the limited board space and the additional costs led us to conclude a hot-swap controller would be superfluous for a single module. Reverse polarity protection was only considered after rediscovering some discourse on how some SSDV2 failures were allegedly attributed to reverse polarity. The decision to include RPP in the final design came after reading some reverse polarity failures in the Open Source DC/DC Converter project by Rootthecause (see Further Reading).

The v5 still had proper reverse polarity protection. However, all successors no longer did (only the intrinsic body diodes). Since the space requirement and (depending on the implementation) loss of power could not be combined with the goals and the installation was not intended for technical laymen anyway, it was omitted. Both the v8 and the v9-1 were connected with reversed polarity due to a series of errors. In both cases, the HV fuse tripped via the body diode. In the v8, the precharge IGBT was also destroyed, but worked again after it was replaced. In the v9-1, the low-side FET was permanently conductive, but even after replacing it, no problems occurred in this context in the following months.

Our risk assessment for the SSDV3 project expressly excluded an input fuse, since the risk of a false-trip during flight causing loss-of-signal and uncontrolled flyaway would be much more hazardous than a localized electrical fault. UBCO Aerospace has also had its own history of reverse polarity faults, so an RPP circuit was considered as the minimum protective circuitry to be added to the project. And distributor pricing had 100 V P-FETs as more expensive than a LM5050-1 + N-FET design, so the latter was chosen.

The reverse polarity protection uses an example circuit shown in Section 8.2.6 of the LM5050-1 datasheet [35], and is illustrated in Figure 4.8. While the LM5050-1 is intended as an ideal diode controller, its purpose in this circuit is to drive the N-channel MOSFET during regular operation. The working principle of the circuit is that the internal body diode of the Q1 MOSFET allows the LM5050-1 and downstream buck converter to power on, then the LM5050-1 turns on Q1 to allow for conduction through the FET N-channel region rather than the body diode.

In the event of reverse polarity on VBAT, 50 V is now connected to the PGND net. The diode network D2 prevents backwards conduction through U1, and the body diode of Q1 blocks significant backwards conduction through the downstream buck converter. Some necessary conduction still occurs to the VIN net via the internal body diodes of the power stage MOSFETs, which replaces the D2 SMBJ60A diode shown in Figure 31 of [35] operating in forward conduction during reverse polarity.

Last Revised 2026-05 | PUBLIC RELEASE – CC SA-BY-4.0 | Page 29/50

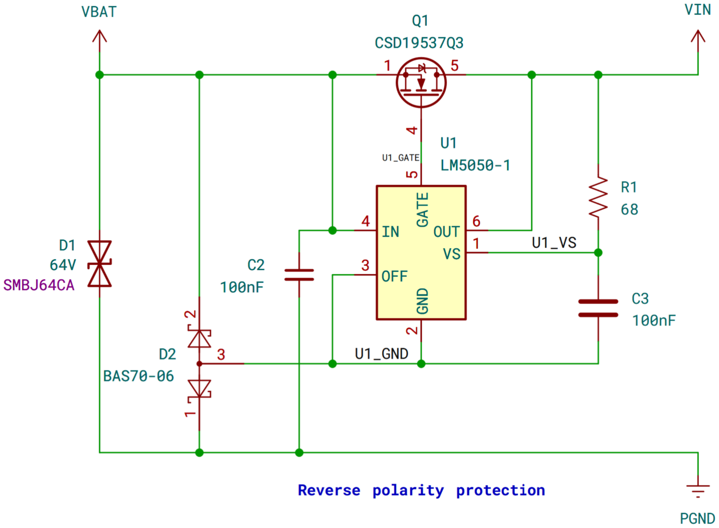
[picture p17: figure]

Figure 4.8: The reverse polarity protection circuit, implemented with the LM5050-1. Though not included, the internal body diodes of the power stage MOSFETs are a part of this circuit.

Since the VIN net is also at 50 V, the LM5050-1 powers on normally, and the U1_GND net’s return path is redirected by the D2 diode network back to the battery through the VBAT net (which is now ground). With the OUT pin having a higher voltage than the IN pin, the LM5050-1 keeps Q1 turned off, fully preventing reverse conduction and ensuring the whole system remains in a well defined state when in reverse polarity.

Why are we using bidirectional TVS diodes before the RPP circuit in contrast to Figure 31 in the LM5050-1 datasheet? Because the bidirectional TVS diodes were the only ones available on LCSC at the desired voltage that had the “basic” assembly costs for JLCPCB.

Page 30/50 | PUBLIC RELEASE – CC SA-BY-4.0 | Last Revised 2026-05

### 5 PCB Design

### 5.1 Board Specifications

A 4-layer, 1 oz/ft

2 copper thickness PCB is used for this design. The typical differential stackup of common 4-layer boards helps reduce the ground return path distance and offers better EMI mitigation compared to a 2-layer board. An aggressive 0.25 mm trace clearance is set to improve manufacturing tolerances, and a 0.5 mm clearance was used on 50 V exterior traces.

The solder joint integrity of the QFN packages used in this design are sensitive to the uneven pads produced by HASL surface finishes [36]. So instead an ENIG surface finish is used.

### 5.2 Grounding

The entire inner layer L1 is used as a unified ground plane, while all other layers use ground-fill to improve the thermal dissipation of the board. Stitching vias are used close to the power stage capacitors to reduce their return path impedance.

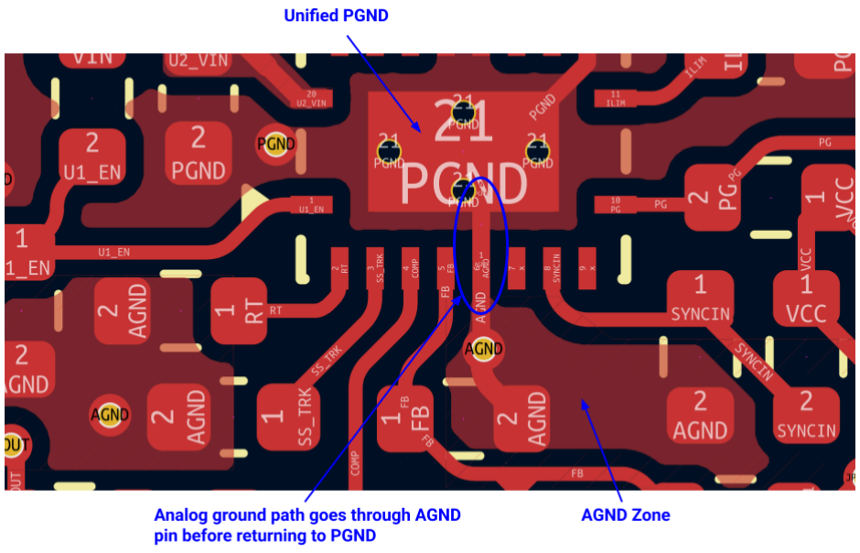
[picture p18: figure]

Figure 5.1: The PGND and AGND routing.

The analog ground net is connected via net-tie to the unified ground plane in close proximity to the LM5146 AGND pin. The purpose of the separate analog and power ground nets is to control the return path of the analog circuits so that they flow through the AGND pin while still remaining connected to the unified power ground plane, as shown in Figure 5.1. They are not separated for the purpose of complete circuit separation [37].

Last Revised 2026-05 | PUBLIC RELEASE – CC SA-BY-4.0 | Page 31/50

### 5.3 High-frequency Power Loop

The LM5146 datasheet (in Figure 11-1 of [4]) and numerous application notes emphasize the importance of proper layout for the buck converter power stage, mainly as the primary method for minimizing the system’s conducted and radiated EMI. While the anticipated EMI spectrum from this buck converter is not a major concern in drone applications, it is still important to manage the power stage layout to control the switch-node ringing and leading-edge voltage peaking caused by parasitics. Furthermore, the fast dv/dt switching can also induce “phantom turn-on,” where the low-side MOSFET gate voltage is momentarily forced high through drain-gate coupling of the MOSFET miller capacitance, causing it to turn on and result in high-current shoot-through events [38]. The implemented layout is shown in Figure 5.2.

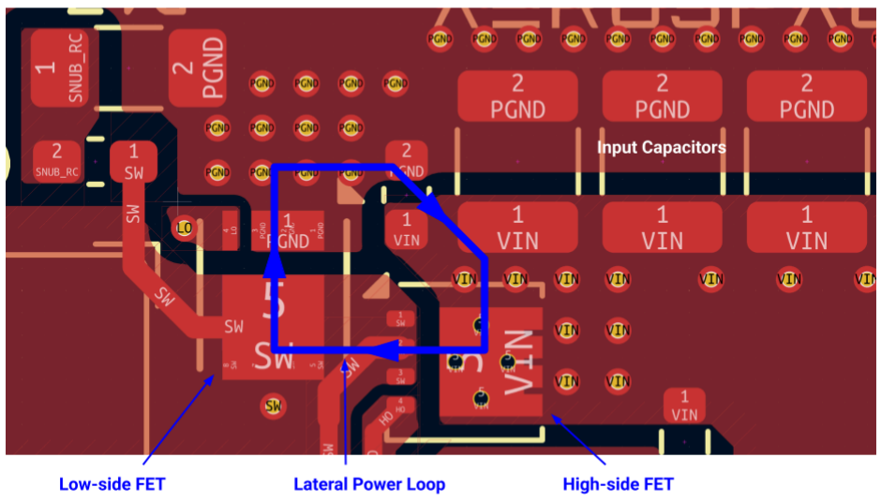
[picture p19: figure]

Figure 5.2: The MOSFET placement and power loop.

The SSDV3 Rev. C layout uses the “improved lateral switching loop design” discussed in [39], where the MOSFETs are placed perpendicular to each other. The particular selected MOSFETs use 3.3 × 3.3 mm PQFN packages that are smaller than the popular 5 × 6 mm SON “SuperSO-8” packages, allowing for a more compact arrangement. Combined with a 0603 ceramic capacitor between the two MOSFETs for high-frequency decoupling, the resulting enclosed area of the lateral switching power loop is kept to a minimum.

If the power stage layout design fails, and the switch-node ringing is still unsatisfactory, a basic RC snubber circuit has been included in the design whose components are to be added experimentally in testing to reduce ringing. A 0 Ω 1206 resistor is used to connect the snubber copper island to ground, preventing the unused snubber copper from floating.

Page 32/50 | PUBLIC RELEASE – CC SA-BY-4.0 | Last Revised 2026-05

In a similar fashion, the gate driver circuitry from the LM5146 to the MOSFETs is sensitive to the PCB design. Because of the LM5146’s ability to source and sink 2-3 A to and from the MOSFET gate in the span of nanoseconds, parasitic inductance in the gate driver path can cause slower turn-on times and unwanted ringing. Usual advice to mitigate the latter is to use gate resistors to dampen any ringing, yet carries the downside of further slowing the MOSFET turn-on times and introduces losses. The SSDV3 Rev. C already features a resistor in the bootstrap circuit to slow the turn-on of the high-side MOSFET, so adding gate resistors would be redundant and counterproductive. Instead, the PCB design focuses on minimizing the parasitic inductance in the gate driver path using the layout shown in Figure 5.3.

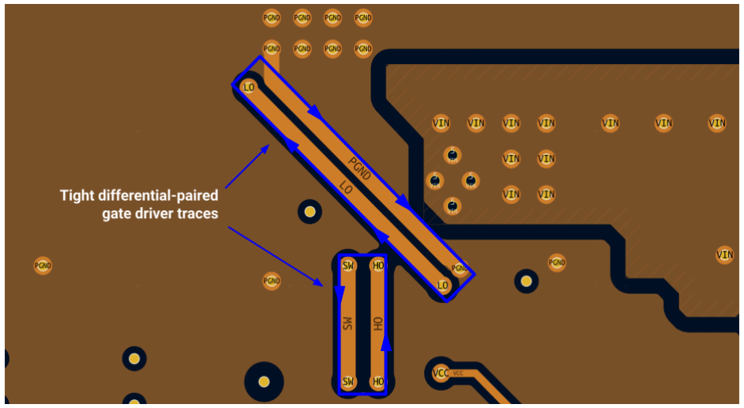
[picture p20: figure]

Figure 5.3: The gate driver trace routing on the internal layer L2.

The LM5146 has been placed close to the power stage to keep the connections to the MOSFETs short. The high- and low-side gate drivers are routed differentially with their corresponding return paths (the switch-node and ground, respectively) to minimize their loop inductance. Wide 0.5 mm traces ensure the resistance from the gate driver to the MOSFETs is kept low, maximizing the gate drive strength from the LM5146.

### 5.4 Inrush Current Mitigation

The potential damage caused by inrush current is mitigated primarily through extra large copper pours leading to and from the buck converter input capacitors. The width of the copper leading from the battery input pads are at least in excess of 4.00 mm, providing a large copper cross-section for conduction through the whole return path for the inrush current.

Review of the HW-636 copper trace explosions also suggested that resonance in the wires leading to the module increased the net energy dissipation in sensitive areas and contributed to

Last Revised 2026-05 | PUBLIC RELEASE – CC SA-BY-4.0 | Page 33/50

its failure. A 47 μF electrolytic capacitor is added to the input as a means to dampen these resonances.

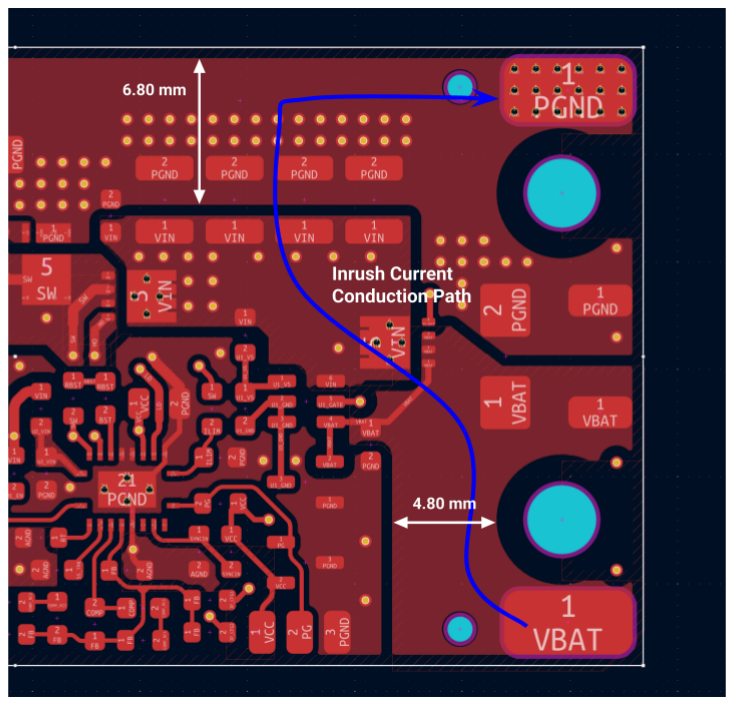
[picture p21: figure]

Figure 5.4: The reinforced copper pours to mitigate inrush current.

### 5.5 Component Footprint Design

The baseline footprints for both the Infineon and TI MOSFETs are based on the manufacturer provided footprints from UltraLibrarian. The BSZ096N10LS5 footprint was modified to improve copper clearances, while the CSD19537Q3 and LM5146 footprints have added 0.3 mm thermal vias under the exposed pad.

### 5.6 Connectors

The power connections are made with simple copper pads for wires to be directly soldered on to. This was a compromise to allow the design to remain connector-agnostic during its evaluation. The use of a terminal block on the output was intentionally avoided since it was a common failure point for the team in 2024, and common blocks are typically not rated for above 3 A.

Page 34/50 | PUBLIC RELEASE – CC SA-BY-4.0 | Last Revised 2026-05

### 6 Testing and Verification

### 6.1 Testing Notes and Limitations

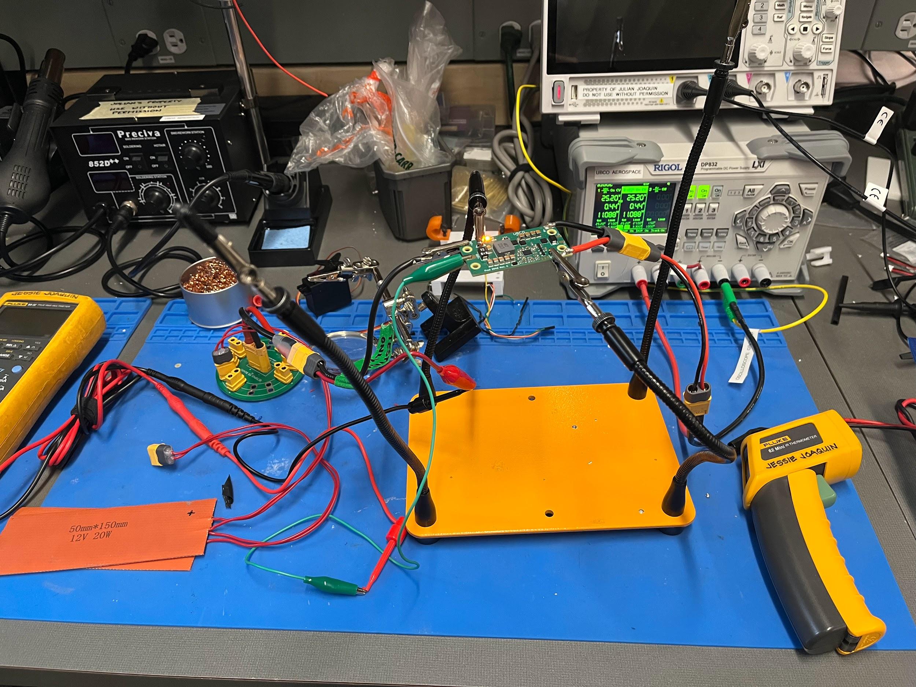
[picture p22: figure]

FIgure 6.1: The test rig used for measuring regulation under load and thermal characteristics.

- UBCO Aerospace does not have access to a professional electronic load, so we had to get creative when it came to performing load tests. For DC loads, we had seven heating pads on hand and decided to use them as incremental loads. Each heating pad was intended for 20 W at 12 V, or in other words had a resistance of 7.2 Ω. Though this number seemed to vary wildly in testing, and we often saw the resistance be in the higher ranges of 8.0 Ω. Put all seven in parallel, and the smallest possible load resistance is about 1.15 Ω. This was the limiting factor for all our load testing, and why the 5.1 V and 7.4 V performance curves in Section 1.3 don’t extend all the way to 8 A.
- For transient load testing, we created a fairly simple, makeshift circuit using a 555 timer, one typical IRFZ44N MOSFET, and some cheap low-value resistors. The system-level circuit is shown in Figure 6.2. A simple monostable multivibrator drives a MOSFET for about one second and provides a conduction path through a 1 Ω, 20 W-rated resistor. A 0.1 Ω low-side resistor is used for shunt-based current sensing via an oscilloscope. The limited power rating constrained our transient load testing to only the 5.1 V output.
Last Revised 2026-05 | PUBLIC RELEASE – CC SA-BY-4.0 | Page 35/50

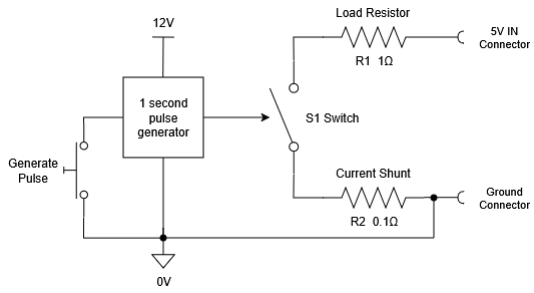
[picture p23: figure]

Figure 6.2: The makeshift transient load tester.

- DC load current measurement was conducted using a Fluke 89 IV multimeter with some very shoddy alligator clip test wires. Input current was simply read from the display of a RIGOL DP832 test bench power supply with a limited resolution of 0.01 A.
- Temperature measurements were taken from a Fluke 62 Mini IR thermometer. In order to precisely measure the temperature of the MOSFET packages, the thermometer had to be held mere millimeters above the device under test. At this distance, it was difficult to gauge what exactly the thermometer was measuring since the built-in laser pointer was intended for distances in meters, not millimeters, and was significantly offset from the actual measurement position at such close distances.
- Inrush current survival testing was conducted using a Jesverty SPS-6005N power supply with its manufacturer-provided 12 inch alligator clip wires. It has a measured capacitance of 5.29 mF across the output terminals. The supply would be operating at 50 V, 1 A, and powering the SSDV3. To simulate a hot-plug event with a LiPo battery, the positive banana plug to the supply would be disconnected and reconnected. The supply exhibited some unusual behaviour where the output would be briefly clamped to below 40 V after reconnection, and then return to 50 V shortly after, as shown in Figure 6.3.
- The fast switching rise times introduced noticeable coupling into the oscilloscope measurements throughout testing. At some point, we had mounted the oscilloscope probe’s 3 inch ground wire some distance away from the switch-node trace when attempting to measure the switching waveforms. The observed waveforms showed major +10 V overshoot on the switching rising edge, alongside some very visible ringing in the tens of megahertz. It took a while to realize the waveforms did not reflect the actual switching voltage, and we relocated the probe ground wire to a closer ground node to finally get the waveforms seen in Figures 1.8 and 1.9. Keep your probe ground wires close to your measurement points!
Page 36/50 | PUBLIC RELEASE – CC SA-BY-4.0 | Last Revised 2026-05

Figure 6.3: The SSDV3 input voltage with the SPS-6005N power supply during a simulated hot-plug.

### 6.2 Testing Procedures

The following test processes define the methods used to characterize the SSDV3 Rev. C prototype and verify the functional requirements listed in Section 4.1. These procedures are not exhaustive for the full breadth of testing for the project, and only detail the prototype-level tests performed with the equipment available to ensure the design meets its requirements. Some procedures have been excluded for brevity. Each procedure identifies the controlled variables, measured quantities, equipment, setup, and expected outputs used later in the requirement verification matrix.

### 6.2.1 DUT Description

The device under test (DUT) is a single assembled SSDV3 Rev. C module with short wires connected to their respective input and output solder pads. XT60 connectors and alligator clips were used as interfaces for testing.

Last Revised 2026-05 | PUBLIC RELEASE – CC SA-BY-4.0 | Page 37/50

### 6.2.2 Load Sweep Test

Procedure ID | P-2
Independent Variables | Constant input voltage VIN. Load resistance RL , and in turn output current IOUT.
Dependent Variables | Input current IIN, output voltage VOUT, and peak-to-peak output ripple ṽOUT.
Equipment | 1. DUT, SSDV3 Rev. C 2. Power supply, RIGOL DP832 3. Oscilloscope, RIGOL DHO804 4. Multimeter, Fluke 89 IV 5. Electronic Load, 20-W thermal pads ×7

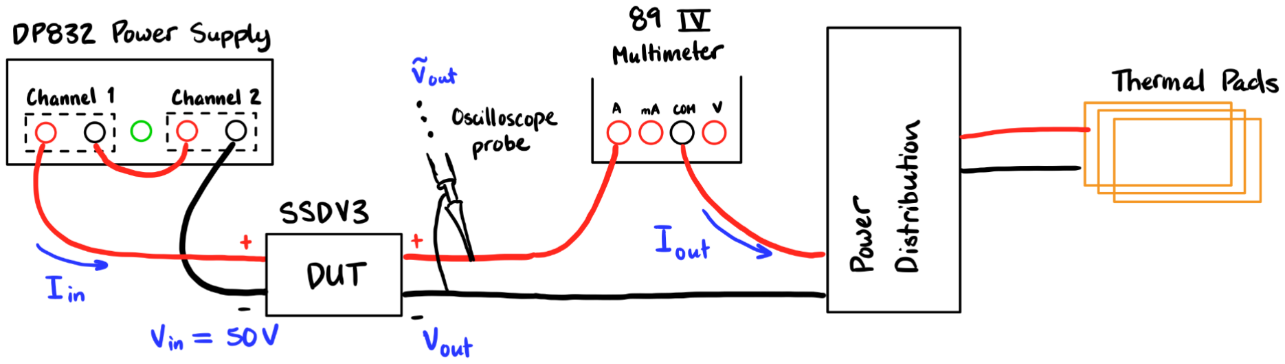
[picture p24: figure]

Setup | Figure 6.4: The load sweep test setup. 1. Set the power supply output and connect it to the DUT input. 2. Connect the multimeter as an ammeter to the positive DUT output. 3. Connect an oscilloscope probe to measure the DUT output. 4. Connect the electronic load to the DUT output.

Procedure

1. Configure the SSDV3 DUT to 5.1 V and connect it to the test setup.
2. Set the power supply output to 50 V, 3 A.
3. Set the multimeter to measure current.
4. Start with zero connected thermal pads.
5. Measure the VIN, IIN, VOUT, peak-to-peak ṽOUT, and IOUT.
6. If the output power is near or exceeding 100 W, or if there are no more thermal pads available, continue to step 7. Otherwise increment the load by adding another parallel thermal pad and return to step 5.
7. Repeat steps 4 through 6, first by removing and configuring the SSDV3 DUT for 7.4 V or 12 V, then by reattaching the DUT to the test setup and continue testing.
8. Use the measured values to calculate efficiency ŋ and power loss PLOSS for all IOUT.

Outcomes

Load regulation VOUT vs. IOUT, output ripple ṽOUT vs. IOUT, efficiency ŋ vs. IOUT, and power loss PLOSS vs. IOUT.
Table 6.1: Load Sweep Testing Procedure.
Page 38/50 | PUBLIC RELEASE – CC SA-BY-4.0 | Last Revised 2026-05

### 6.2.3 Thermal Response Test

Procedure ID | P-3
Independent Variables | Constant input voltage VIN. Output voltage VOUT, load resistance RL , and in turn output current IOUT.
Dependent Variables | Input current IIN, high-side FET temperature THS, and inductor temperature Tind.
Equipment | 1. DUT, SSDV3 Rev. C 2. Power supply, RIGOL DP832 3. Multimeter, Fluke 89 IV 4. Thermal Camera/IR Thermometer, Fluke 62 Mini 5. Electronic Load, 20-W thermal pads ×7

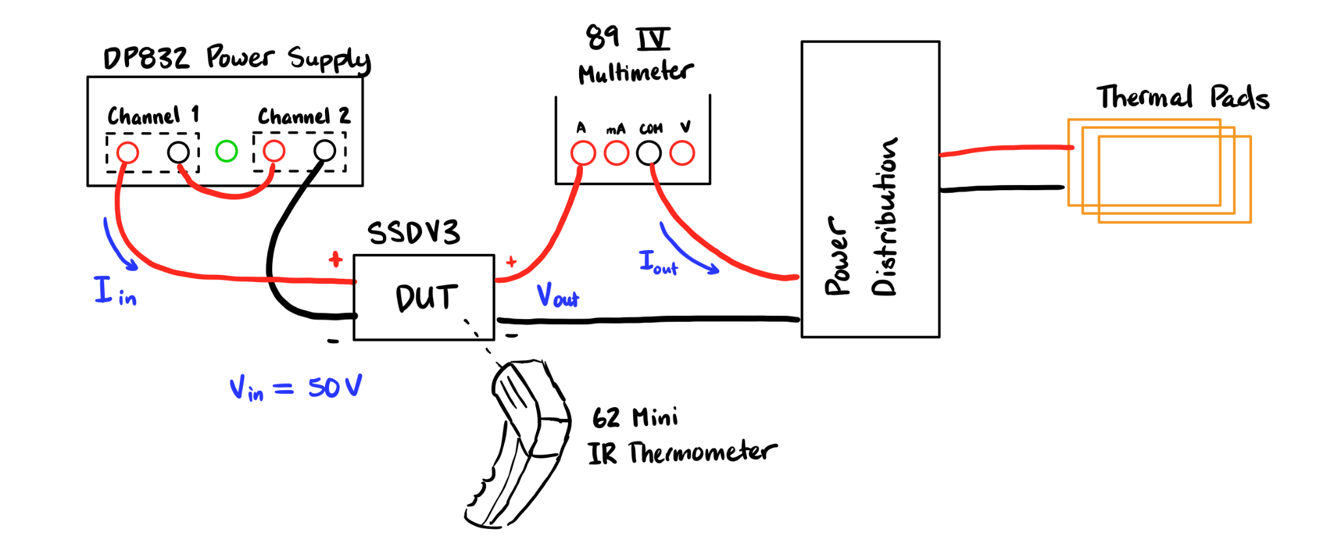
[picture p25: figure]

Setup | Figure 6.5: The thermal response test setup. 1. Set the power supply output and connect it to the DUT input. 2. Connect the multimeter as an ammeter to the positive DUT output. 3. Connect the electronic load to the DUT output.
Procedure | 1. Configure the SSDV3 DUT to the desired output voltage and connect it to the test setup. 2. Set the power supply output to 50 V, 3 A. 3. Set the multimeter to measure current. 4. Connect thermal pads as needed to configure the desired output current. 5. Turn the supply off and wait for the DUT to be at room temperature. 6. Turn on the supply and measure the output current, output voltage, and the HS FET and inductor temperature. Repeat every minute for 15 minutes. 7. Repeat the procedure as necessary for different VOUT and IOUT.
Outcomes | THS vs. time, and Tind vs. time, and THS in typical operation.
Table 6.2: Thermal Response Testing Procedure.
Last Revised 2026-05 | PUBLIC RELEASE – CC SA-BY-4.0 | Page 39/50

### 6.2.4 Load Transient Test

Procedure ID | P-4
Independent Variables | Constant input voltage VIN. Load resistance RL , and in turn output current IOUT.
Dependent Variables | Output voltage VOUT.
Equipment | 1. DUT, SSDV3 Rev. C 2. Power supply, RIGOL DP832 3. Oscilloscope, RIGOL DHO804 4. Electronic Load, Makeshift Load Tester

Setup

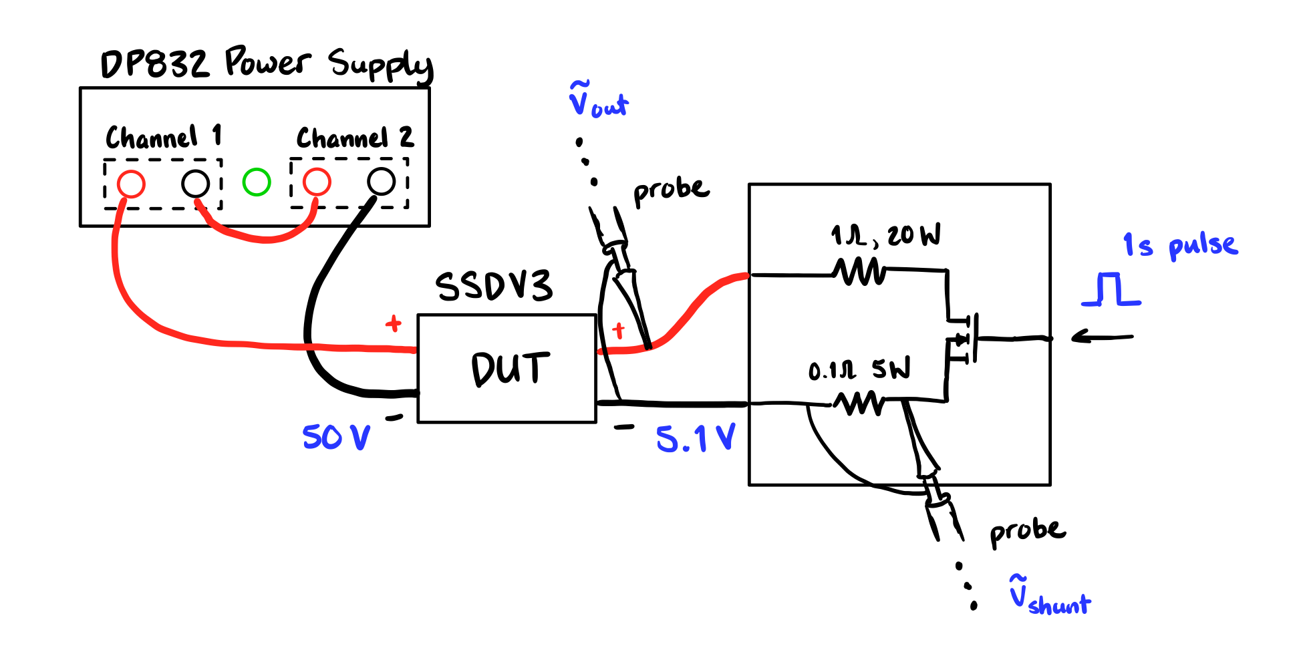
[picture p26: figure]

Figure 6.6: The thermal response test setup.

1. Set the power supply output and connect it to the DUT input.
2. Connect an oscilloscope probe to measure the DUT output. Keep the probe and ground wire as close as possible to the DUT output.
3. Connect the electronic load to the DUT output and electronic load shunt. Keep wires from DUT to electronic load as short as possible.
Procedure | 1. Configure the SSDV3 DUT to the desired output voltage and connect it to the test setup. 2. Set the power supply output to 50 V, 3 A. 3. Set the multimeter to measure current. 4. Use the load tester to induce a load step. 5. Repeat the procedure as necessary for different VOUT and IOUT.
Outcomes | Transient VOUT over/under-shoot and settling time.
Table 6.3: Transient Load Testing Procedure.
Page 40/50 | PUBLIC RELEASE – CC SA-BY-4.0 | Last Revised 2026-05

### 6.2.5 Line Transient Test

Procedure ID | P-5
Independent Variables | Input voltage VIN.
Dependent Variables | Output voltage VOUT.
Equipment | 1. DUT, SSDV3 Rev. C 2. Power supply, RIGOL DP832 3. Oscilloscope, RIGOL DHO804
Setup | 1. Set the power supply output and connect it to the DUT input. 2. Connect an oscilloscope probe to measure the DUT input and output.
Procedure | 1. Set the power supply output to 50 V, 1 A. 2. Program the DP832 to perform a voltage drop to 35 V via the timer function. 3. Enable the timer and supply outputs, and observe VIN and VOUT.
Outcomes | Transient VOUT.
Table 6.4: Line Transient Testing Procedure.

### 6.2.6 Inrush Current Survival Test

Procedure ID | P-6
Independent Variables | Constant input voltage VIN and output voltage VOUT.
Dependent Variables | DUT operability.
Equipment | 1. DUT, SSDV3 Rev. C 2. Power supply, Jesverty SPS-6005N
Setup | 1. Set the power supply output and connect it to the DUT input.
Procedure | 1. Set the power supply output to 50 V, 1 A. 2. Remove the positive wire banana plug from the supply, then quickly reconnect it. Rapid reconnection may produce arcing at the connector and should only be performed with current limiting enabled and appropriate precautions.
Outcomes | DUT tolerance for inrush current.
Table 6.5: Inrush Current Survival Testing Procedure.
Last Revised 2026-05 | PUBLIC RELEASE – CC SA-BY-4.0 | Page 41/50

SSDV3 Rev. C Documentation

### 6.3 Requirement Verification

Requirement ID | Requirement Statement | Verification Success Criteria | Verification Procedure | Verification Results | Requirement Status
R-1 | The SSDV3 shall accept 6S and 12S battery input. | ● Operable across DC input sweep from 20 V to 60 V | Informal | ● Tested at 25 V and 50 V ● No full DC input sweep | Partial
R-2 | The SSDV3 shall provide selectable regulated voltage outputs of 5.1 V, 7.4 V, and 12 V. | ● Functioning voltage setting jumpers | Informal | ● Operable with measured 5.1 V, 7.4 V, and 12 V output | Pass
R-3 | The SSDV3 shall provide a nominal output current of 5 A and a maximum output current of 8 A. | ● DC load sweep for all output voltages from 0 to 8 A ● FET temperatures do not exceed limits enforced by R-5 | P-2 | ● Capable of 5 A output with all output voltages ● Cannot sustain 8 A output due to thermal limit ● Cannot measure 8 A output for 5.1 V and 7.4 V due to load limitations ● Thermal derating required based on output voltage | Partial
R-4 | The SSDV3 shall maintain its regulated voltage with no more than 5% deviation. | ● VOUT sag with heavy load is less than 1% ● VOUT overshoot during load-off is less than 5% ● VOUT undershoot during line transient is less than 5% | P-2 P-4 P-5 | ● VOUT deviates less than 1% with DC load ● VOUT deviates less than 3% with 5 A load step ● No observed deviation with line transients | Pass

Table 6.6A: Requirements Verification Matrix, R-1 through R-4.

Page 42/50 | PUBLIC RELEASE – CC SA-BY-4.0 | Last Revised 2026-05

SSDV3 Rev. C Documentation

Requirement ID | Requirement Statement | Verification Success Criteria | Verification Procedure | Verification Results | Requirement Status
R-5 | The SSDV3 shall limit its MOSFET junction temperature rise to no more than 80 °C. | ● Components can survive +80 °C rise above typical ambient of 21 °C ● Measured FET temperature rise does not exceed +80 °C | P-3 | ● Some parts limited to 85 °C temperature ● Measured ΔTJ exceeds +80 °C at VOUT = 12 V, IOUT ≥ 5 A | Fail
R-6 | The SSDV3 shall survive typical 50 V hot-plug events for UAV applications. | ● Operable after hot-plug into battery or supply | P-6 | ● Operable after rapid reconnect with supply at 25 V and 50 V ● Operable after typical 12S LiPo battery insertion | Pass
R-7 | The SSDV3 shall protect downstream electronics from short-circuit faults. | ● OCP clamps output current or outright disables output | Informal | ● OCP active during short-circuit event, output disabled | Pass
R-8 | The SSDV3 shall be no larger than the SSDV2. | ● Measured dimensions within specification | Informal | ● Smaller by design | Pass

Table 6.6B: Requirements Verification Matrix, R-5 through R-8.

Last Revised 2026-05 | PUBLIC RELEASE – CC SA-BY-4.0 | Page 43/50

### 7 Discussion

### 7.1 Next Revision

- More thermal mitigation is needed. Heat output from the module is the present limiting factor for the maximum power output, and it is causing the design to fall short of its target output current. This will involve using higher temperature-rated components (e.g. X7R capacitors instead of X5R) and reducing the power loss of the current design when under load. The primary source of loss right now is through inductor hysteresis loss, which is both much higher than expected and remains unquantified with the current design. There may also be a possibility of reducing the switching frequency to decrease tertiary switching losses.
- Eventually, the design should not require a heatsink. While it seems counterproductive to the prior statement, the use of a heatsink has introduced some mounting challenges that restrict the universality of the design for drone applications. The 1/8th brick-style hole arrangement in particular is not friendly to any common FPV drone screw grids, something only we’ve solved by using 3D-printed mounts. Many colleagues would also like to eventually be able to encapsulate the module in heat-shrink. Maybe it’s possible?
- Better connectors are needed on the PCB, as solder pads do not provide any isolation. The idea of using solder pads originated from how most drone ESCs and BECs have directly soldered wires to the PCB. But with the sheer wiring complexity of many of our projects at UBCO Aerospace, the lack of a physical barrier to the conductive parts of the connections has posed a serious risk should a wire come loose. We’ve had to compensate for this by using a variety of mitigation techniques to prevent conduction never done before in this club, as discussed in the Installation Guidelines. While those guidelines are generally good practice, the design should not have to rely on those practices to achieve safe isolation at the current operating voltage. Additionally, the placement of the solder pads involves non-negligible separation in the power wires, introducing unnecessary loop inductance at both the input and output. So something like an XT30PW connector will be welcome.
- The output ripple shown in Figure 1.6 and 1.7 have a significant ESL spike component in their waveforms, likely tied to the distant placement of the output capacitors away from the low-side MOSFET source pin. Future revisions will need to find a way to reduce the loop inductance of the output capacitors.
- Fix the electrolytic input cap so it’s protected by RPP!
- Change out the D2 BAS70-06 diode in the RPP circuit for 100 V-rated diodes.
Page 44/50 | PUBLIC RELEASE – CC SA-BY-4.0 | Last Revised 2026-05

### 7.2 Cut Content

This is material that didn’t really fit in any particular section but is still worth discussing.

- The Rev. C design back in September of 2025 was only intended to be a prototype/testbed for further development, while the Rev. D design would be fully geared towards deployment for UBCO Aerospace. When this project started, it was not even guaranteed the design would be produced since we were more focused on looking for more commercial alternatives to the failed modules discussed in Section 3.1. Our goals shifted once it was realized the Rev. C design would be feasible, and it was rushed into service so that testing of the Jellyfish competition aircraft could fully commence by November. Nonetheless there were many lessons learned from the design that will motivate changes in the next revision.
- During the first tests, the 3 inch ground wire of an oscilloscope probe was accidentally shorted with the solder terminal of one of the 50 V ceramic input capacitors. Thankfully the overcurrent protection was active on the test bench supply at the time, and only a very brief spark occurred between the wire and the capacitor. This did cause minor charring on the capacitor, but we neglected it and testing continued. Two weeks later, the same module entered a short-circuit failure 4 minutes and 37 seconds into a thermal test. It took about a week to figure out the ceramic input capacitor had been seriously damaged, and the thermal testing had caused internal cracks to worsen, leading to the corner of the capacitor to explode. The damage can be seen in Figure 7.1 and Figure 7.2. The module worked fine after replacing the damaged capacitor, but the whole ordeal shows how sensitive ceramic capacitors are to fracture.
Last Revised 2026-05 | PUBLIC RELEASE – CC SA-BY-4.0 | Page 45/50

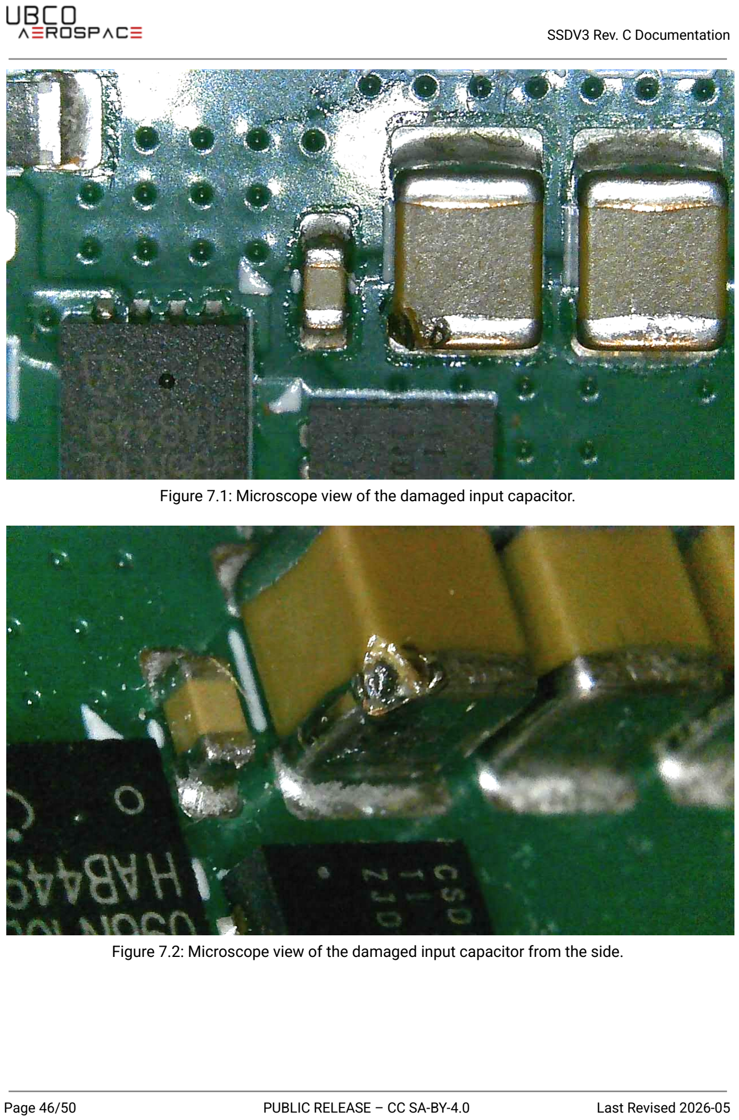
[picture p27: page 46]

Figure 7.1: Microscope view of the damaged input capacitor.

Figure 7.2: Microscope view of the damaged input capacitor from the side.

Page 46/50 | PUBLIC RELEASE – CC SA-BY-4.0 | Last Revised 2026-05

### 8 References

[1] A. Lopez and R. Ajani, “Controller to Converter – Design Considerations for 24V and 48V Systems,” Texas Instruments, SNVAAA7, Oct. 2024. Available: https://www.ti.com/lit/an/snvaaa7/snvaaa7.pdf
[2] O. Guillemant, “RAQ Issue 199: Three Compact Solutions for High Step-Down Voltage Ratios,” Analog Dialogue, vol. 56, no. 1, Mar 2022. [Online]. Available: https://www.analog.com/en/resources/analog-dialogue/raqs/raq-issue-199.html
[3] A. Bindra, “The Advantages of Designing Multiphase, High-Power Buck Converters,” DigiKey, Feb. 05, 2013. Available:
https://www.digikey.ca/en/articles/the-advantages-of-designing-multiphase-highpower-buck-con verters (https://www.digikey.ca/en/articles/the-advantages-of-designing-multiphase-highpower-buck-converters)
[4] Texas Instruments, “LM5146 100-V Synchronous Buck DC/DC Controller With Wide Duty Cycle Range,” SNVSBV0A, Jun. 2021. [Online]. Available: https://www.ti.com/lit/gpn/lm5146
[5] Texas Instruments, “LM5148 80-V, Synchronous, Buck DC/DC Controller with Ultra-Low IQ and Dual Random Spread Spectrum,” SNVSC01, Feb. 2023. [Online]. Available: https://www.ti.com/lit/gpn/lm5148
[6] R. Mammano, “Switching Power Supply Topology: Voltage Mode vs. Current Mode,” Unitrode Corporation, DN-62, 1994. [Online]. Available: https://www.ti.com/lit/pdf/slua119
[7] S. Maniktala, “Voltage-Mode, Current-Mode (and Hysteretic Control),” Microsemi Corporation, TN-206, 2012. [Online]. Available: https://www.microchip.com/content/dam/mchp/documents/PMIC/ApplicationNotes/ApplicationNotes/DCDC_TN_206.pdf (https://www.microchip.com/content/dam/mchp/documents/PMIC/ApplicationNotes/ApplicationNotes/DCDC_TN_206.pdf)
[8] M. Nogawa, “Fixed Frequency Control vs Constant On-Time Control of Step-Down Converters,” Texas Instruments, 2016.
https://www.ti.com.cn/content/dam/videos/external-videos/en-us/1/3816841626001/5103393152001.mp4/subassets/fixed-frequency-vs-constant-on-time-control-of-dcdc-conver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 (https://www.ti.com.cn/content/dam/videos/external-videos/en-us/1/3816841626001/5103393152001.mp4/subassets/fixed-frequency-vs-constant-on-time-control-of-dcdc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)
[9] L. H. Dixon, “Control Loop Cookbook,” Unitrode Corporation, SLUP113, 1996. [Online]. Available: https://e2e.ti.com/cfs-file/__key/communityserver-discussions-components-files/196/control-loop-cookbook_5F00_slup113.pdf (https://e2e.ti.com/cfs-file/__key/communityserver-discussions-components-files/196/control-loop-cookbook_5F00_slup113.pdf)
[10] R. Taylor, “Power tips: Voltage Mode or Current Mode?,” Texas Instruments, SSZTC38, Oct. 2015. [Online]. Available: https://www.ti.com/lit/pdf/ssztc38
[11] H. Zhang, “Basic Concepts of Linear Regulator and Switching Mode Power Supplies,” Linear Technology Corporation, AN-140, Oct. 2013. [Online]. Available: https://www.analog.com/en/resources/app-notes/an-140.html
[12] T. Stewart, “Current mode control vs Voltage mode control,” Electrical Engineering Stack Exchange, Oct. 2024. https://electronics.stackexchange.com/a/727152
[13] D. Perreault, “Lecture 27: Current-Mode Control,” MIT OpenCourseWare, YouTube. Jul. 17, 2024. [Online]. Available: https://youtu.be/WJNPGXivqew
Last Revised 2026-05 | PUBLIC RELEASE – CC SA-BY-4.0 | Page 47/50

[14] T. Hegarthy, “Voltage-mode control and compensation: Intricacies for buck regulators,” EDN, Jun. 30, 2008.
https://www.edn.com/voltage-mode-control-and-compensation-intricacies-for-buck-regulators/
[15] Texas Instruments, “Buck Converter Modeling, Control, and Compensator Design,” 2008. https://e2e.ti.com/cfs-file/__key/communityserver-discussions-components-files/188/Buck-Converter-Modeling_2C00_-Control_2C00_and-Compensator-Design.pdf (https://e2e.ti.com/cfs-file/__key/communityserver-discussions-components-files/188/Buck-Converter-Modeling_2C00_-Control_2C00_and-Compensator-Design.pdf)
[16] D. Meeks, “Loop stability Analysis of voltage mode buck regulator with different output capacitor types – continuous and discontinuous modes,” Texas Instruments, SLVA301, Apr. 2008. [Online]. Available: https://www.ti.com/lit/pdf/slva301
[17] R. Sheehan, “Understanding and Applying Current-Mode Control Theory,” National Semiconductor Corp., SNVA555, Oct. 31, 2007. [Online]. Available: https://www.ti.com/lit/pdf/snva555
[18] C. Basso, “A tutorial introduction to switching converters,” Future Electronics, Mar. 2023. https://powersimtof.com/Downloads/PPTs/Introduction%20SMPS%20Rev%200.32.pdf
[19] D. W. Hart, Power Electronics. McGraw-Hill Education, 2011.
[20] B. Hauke, “Basic calculation of a buck converter’s power stage,” Texas Instruments, SLVA477B, Dec. 2011. [Online]. Available: https://www.ti.com/lit/pdf/slva477b
[21] B. Barr, “How to select a MOSFET – switch mode power supply,” Texas Instruments, SSZT810, 2018. [Online]. Available: https://www.ti.com/lit/pdf/sszt810
[22] P. B. Green, S. Mazze, O. Guillemant, C. Moesslacher, K. Ream, “OptiMOS

TM device selection for
synchronous rectification,” Infineon Technologies, AN_2212_PL15_2301_094414, Feb. 2023. [Online]. Available:
https://www.infineon.com/assets/row/public/documents/24/42/infineon-mosfet-optimos-devic e-selection-for-synchronous-rectification-applicationnotes-en.pdf (https://www.infineon.com/assets/row/public/documents/24/42/infineon-mosfet-optimos-device-selection-for-synchronous-rectification-applicationnotes-en.pdf)
[23] X. He, D. Li, V. Zhang, “An accurate approach for calculating the efficiency of a synchronous buck converter using the MOSFET plateau voltage,” Texas Instruments, SLVAEQ9, 2020. [Online]. Available: https://www.ti.com/lit/pdf/slvaeq9
[24] B. Barr, “Understanding MOSFET Data Sheets, Part 5 – Switching Parameters,” Texas Instruments, SSZTCH1, Jul. 2015. [Online]. Available: https://www.ti.com/lit/pdf/ssztch1
[25] Infineon Technologies, “BSZ096N10LS5,” 2020. [Online]. Available: https://www.infineon.com/assets/row/public/documents/24/49/infineon-bsz096n10ls5-datashe et-en.pdf (https://www.infineon.com/assets/row/public/documents/24/49/infineon-bsz096n10ls5-datasheet-en.pdf)
[26] Texas Instruments, “CSD19537Q3 100-V N-Channel NexFET™ Power MOSFET,” 2015. [Online]. Available: https://www.ti.com/lit/gpn/csd19537q3
[27] T. Hegarthy, “Powering drones with a wide VIN DC/DC converter,” Texas Instruments, SNVA806A, Nov. 2017. [Online]. Available: https://www.ti.com/lit/pdf/snva806a
[28] E. Falco, “Impact of output capacitor on feedback loop stability of a power supply,” Würth Elektronik, ANP117e, 2024. [Online]. Available: https://www.we-online.com/components/products/media/799539
Page 48/50 | PUBLIC RELEASE – CC SA-BY-4.0 | Last Revised 2026-05

[29] P. Alcorn, “EVGA says Nvidia RTX 3080 cap issues caused crashes, confirms stability issues,” Tom’s Hardware, Sep. 26, 2020. Available: https://www.tomshardware.com/news/evga-nvidia-rtx-3080-capacitor-caused-crashes (https://www.tomshardware.com/news/evga-nvidia-rtx-3080-capacitor-caused-crashes)
[30] J. Wang, H. Zhang, “How to Calculate the Load Pole and ESR Zero When Using Hybrid Output Capacitors,” Texas Instruments, SLVAE26A, 2018. [Online]. Available: https://www.ti.com/lit/pdf/slvae26a/
[31] A. Dahlen, “Guide to Bootstrap Operation in a MOSFET Gate Drive Circuit,” DigiKey, Jul. 16, 2024. [Online]. Available: https://forum.digikey.com/t/guide-to-bootstrap-operation-in-a-mosfet-gate-drive-circuit/43247 (https://forum.digikey.com/t/guide-to-bootstrap-operation-in-a-mosfet-gate-drive-circuit/43247)
[32] R. Manack, R. Taylor, “Controlling switch-node ringing in synchronous buck converters,” Texas Instruments, SLYT465, 2012. [Online]. Available: https://www.ti.com/lit/pdf/slyt465/
[33] S. W. Lee, “Demystifying Type II and Type III Compensators Using Op-Amp and OTA for DC/DC Converters,” Texas Instruments, SLVA662, 2014. [Online]. Available: https://www.ti.com/lit/pdf/slva662/
[34] S. Guinta, “Ask The Applications Engineer–24: Resistance,” Analog Dialogue, vol. 31, no. 1, 1997. [Online]. Available: https://www.analog.com/en/resources/analog-dialogue/articles/ask-the-applications-engineer-24.html (https://www.analog.com/en/resources/analog-dialogue/articles/ask-the-applications-engineer-24.html)
[35] Texas Instruments, “LM5050-1, LM5050-1-Q1 High-Side OR-ing FET Controller,” SNVS629F, 2011. [Online]. Available: https://www.ti.com/lit/gpn/lm5050-1
[36] NXP Semiconductors, “Assembly guidelines for QFN (quad flat no-lead) and SON (small outline no-lead) packages,” AN1902, 2021. [Online]. Available: https://www.nxp.com/docs/en/application-note/AN1902.pdf
[37] Z. Peterson, “AGND vs PGND: Proper Net Tie Connections in Power Regulator PCB Design,” Altium Academy, YouTube. Apr. 17, 2025. [Online]. Available: https://youtu.be/FhnuAaFf2Fg
[38] D. Eagar, “High Power Synchronous Buck Converter Delivers Up to 50A,” Linear Technology Corporation, Design Note 156. [Online]. Available: https://www.analog.com/en/resources/design-notes/synchro-buck-converter-delivers-upto-50a.html (https://www.analog.com/en/resources/design-notes/synchro-buck-converter-delivers-upto-50a.html)
[39] T. Hegarthy, “Improve High-Current DC/DC Regulator EMI Performance for Free With Optimized Power Stage Layout,” Texas Instruments, SNVA803, 2019. [Online]. Available: https://www.ti.com/lit/pdf/snva803/
Last Revised 2026-05 | PUBLIC RELEASE – CC SA-BY-4.0 | Page 49/50

### 9 Further Reading

Influential source material for this project | Notes
Logan Boone Projects | Super Step Down V2 (https://loganbooneprojects.weebly.com/super-step-down-v2.html) | This is the predecessor to the Super Step Down V3 project.
Rootthecause | Open Source DC/DC Converter (https://github.com/Rootthecause/DCDC) | Inspired much of the design process and testing for the project.
Jim Williams | Switching Regulators for Poets - A Gentle Guide for the Trepidatious (https://www.analog.com/media/en/technical-documentation/application-notes/an25fa.pdf) | The app. note might be 40 years old, and some terms are outdated, but it’s fun to read! Plus Appendix C was extremely useful during the design.
Reviews of generic COTS buck converters | Notes
lygte-info.dk | Performance test of Adjustable buck converter LM2596 (https://lygte-info.dk/review/Power%20Adjustable%20buck%20converter%20LM2596%20UK.html)
lygte-info.dk | Test of DC-DC 10A 6.5-60V to 1.25-30V (https://lygte-info.dk/review/Converter%20DC-DC%2010A%206.5-60V%20to%201.25-30V%20UK.html)
lygte-info.dk | Converter DC-DC 3A 4.75-23V to 1.0-17V (http://lygte-info.dk/review/Converter%20DC-DC%203A%204.75-23V%20to%201.0-17V%20UK.html)
Page 50/50 | PUBLIC RELEASE – CC SA-BY-4.0 | Last Revised 2026-05

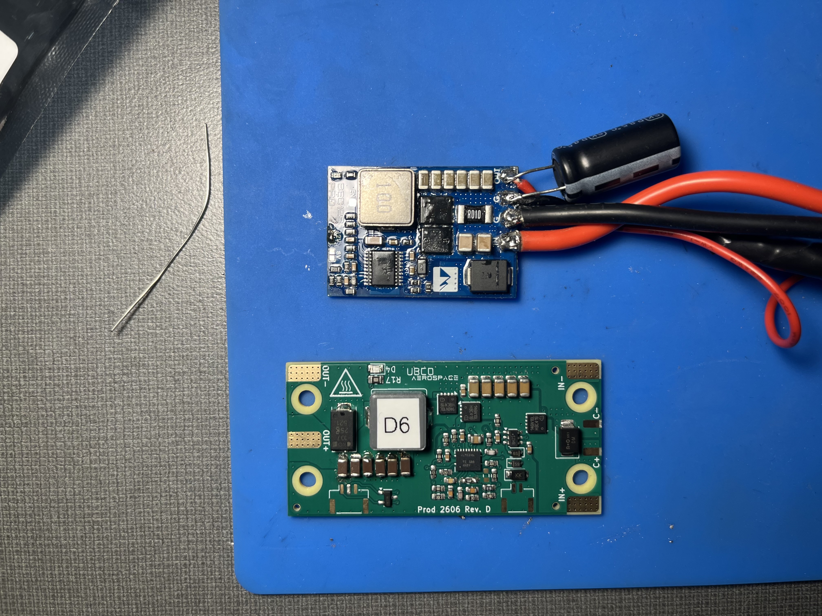
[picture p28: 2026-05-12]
figures/ssdv32602d06_becpro12s_compare.jpeg

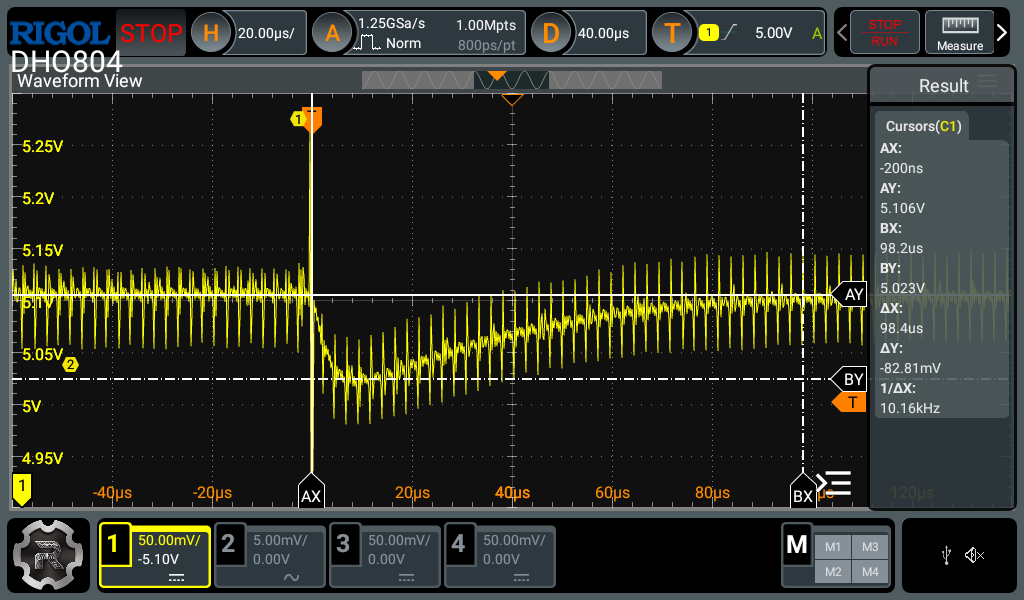
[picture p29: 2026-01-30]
figures/ssdv32542c04_5v_0_5a_trans.png

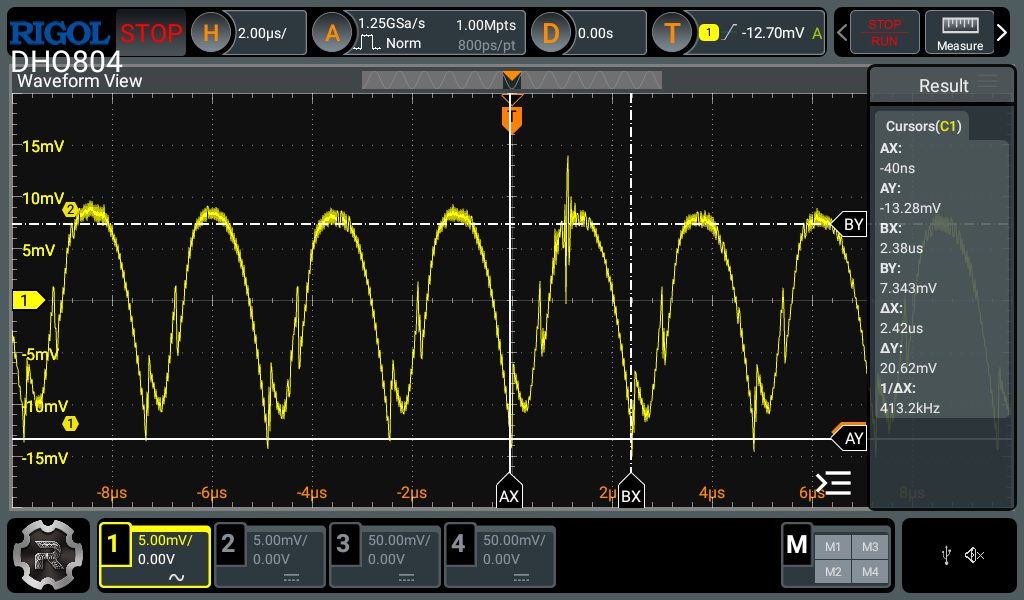
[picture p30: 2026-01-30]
figures/ssdv32542c02_12v_ripple.png

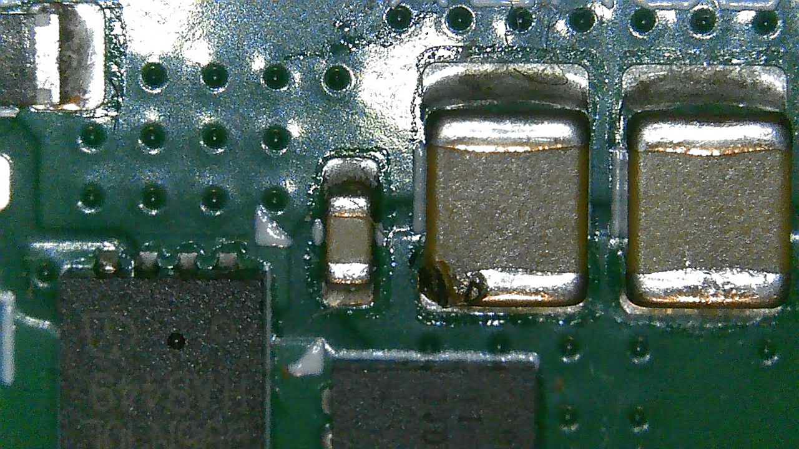
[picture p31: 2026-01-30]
figures/ssdv32542c02_top_20251202.jpg

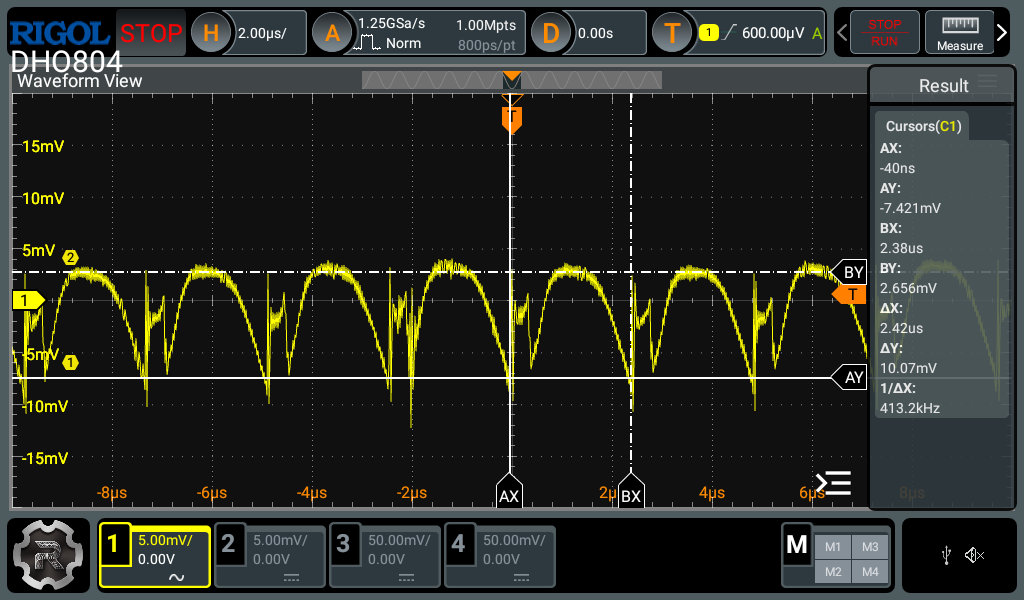
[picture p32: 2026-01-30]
figures/ssdv32542c02_7v4_ripple.png

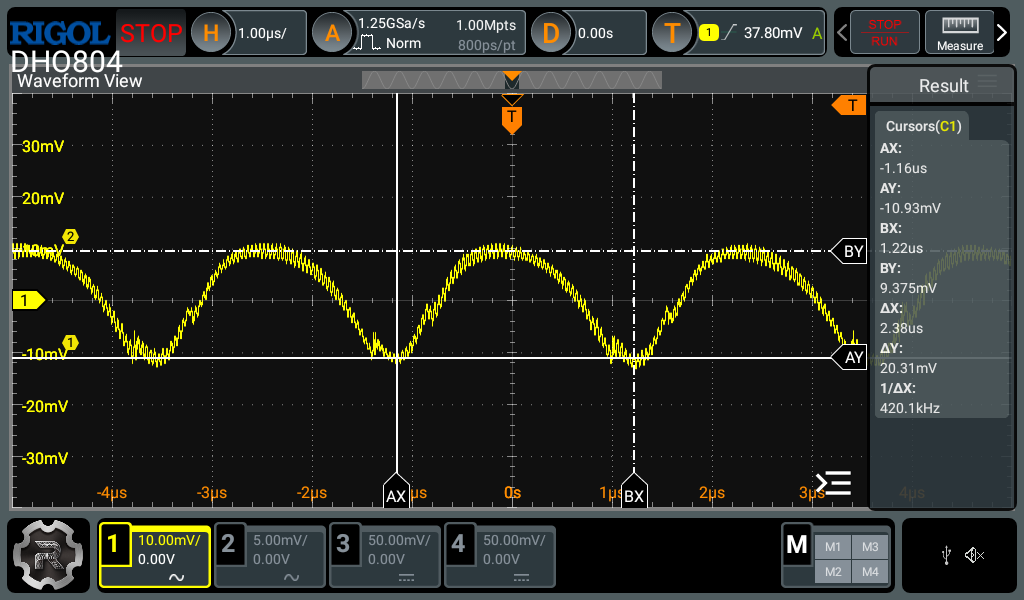
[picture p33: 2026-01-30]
figures/ssdv32542c03_12v_ripple.png

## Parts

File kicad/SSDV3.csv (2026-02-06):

Value | Reference | Footprint | Datasheet | Part Number | Description | LCSC PN | JLCPCB Part Type | Manufacturer
2.2uF | C11 | Capacitor_SMD:C_0805_2012Metric | ~ | GRM21BR71E225KE11L | CAP CER 2.2uF 25V X7R 10% 0805 | C77081 | Extended | Murata Electronics
47nF | C12 | Capacitor_SMD:C_0603_1608Metric | ~ | CL10B473KB8NNNC | CAP CER 47nF 50V X7R 10% 0603 | C1622 | Basic | Panasonic
8.2pF | C14 | Capacitor_SMD:C_0603_1608Metric | ~ | GCM1885C2A8R2DA16D | CAP CER 8.2pF 100V C0G 5% 0603 | C2212506 | Extended | Murata Electronics
1.5nF | C15 | Capacitor_SMD:C_0603_1608Metric | ~ | 0603B152K500NT | CAP CER 1.5nF 50V X7R 10% 0603 | C1595 | Preferred Extended | Guangdong Fenghua
4.7nF | C16 | Capacitor_SMD:C_0603_1608Metric | ~ | 0603B472K500NT | CAP CER 4.7nF 50V X7R 10% 0603 | C53987 | Basic | Guangdong Fenghua
68pF | C17 | Capacitor_SMD:C_0603_1608Metric | ~ | CL10C680JB8NNNC | CAP CER 68pF 50V C0G 5% 0603 | C28262 | Preferred Extended | Panasonic
100uF | C24 | Capacitor_Tantalum_SMD:CP_EIA-7343-20_Kemet-V_HandSolder | https://search.kemet.com/download/specsheet/T521D107M025ATE060 | T521D107M025ATE060 | CAP TANT 100uF 25V 20% 7343 | C212710 | Extended | KEMET
22uF | C18,C19,C20,C21,C22,C23 | Capacitor_SMD:C_1206_3216Metric | ~ | GRM31CC71E226ME15L | CAP CER 22uF 25V X7S 10% 1206 | C5272872 | Extended | Murata Electronics
100nF | C2,C3,C4,C10,C13 | Capacitor_SMD:C_0603_1608Metric | https://www.yageogroup.com/products/Capacitors/part/CC0603KRX7R0BB104 | CC0603KRX7R0BB104 | CAP CER 100nF 100V X7R 10% 0603 | C113803 | Extended | YAGEO
4.7uF | C5,C6,C7,C8,C9 | Capacitor_SMD:C_1206_3216Metric | ~ | GRJ31CZ72A475KE01L | CAP CER 4.7uF 100V X7S 10% 1206 | C3864744 | Extended | Murata Electronics
64V | D1 | Diode_SMD:D_SMB | https://jlcpcb.com/api/file/downloadByFileSystemAccessId/8564879160893476864 | SMBJ64CA | DIODE TVS 64V 600W BI SMB | C41376099 | Preferred Extended | Zhuhai Hongjiacheng
GREEN | D4 | LED_SMD:LED_0805_2012Metric | ~ | KT-0805G | LED GREEN 0805 | C2297 | Basic | Hubei KENTO Electronics
60V | D5 | Diode_SMD:D_SMF | https://jlcpcb.com/api/file/downloadByFileSystemAccessId/8564881124892696576 | SMF60CA | DIODE TVS 60V BI SOD-123FL | C41376092 | Preferred Extended | Zhuhai Hongjiacheng
8V | D6 | Package_TO_SOT_SMD:SOT-23-3 | https://jlcpcb.com/api/file/downloadByFileSystemAccessId/8604441956051673088 | SM08 | DIODE TVS DUAL 8V UNI SOT-23 | C42413902 | Preferred Extended | Zhuhai Hongjiacheng
BAT46WS | D2,D3 | Diode_SMD:D_SOD-323 | ~ | BAT46WS | DIODE SCHOTTKY 100V SOD-323 | C7502692 | Preferred Extended | Zhuhai Hongjiacheng
SM02B-GHS-TB(LF)(SN) | J7 | Connector_JST:JST_GH_SM02B-GHS-TB_1x02-1MP_P1.25mm_Horizontal | ~ | SM02B-GHS-TB(LF)(SN) | CONN 2 POS RIGHT ANGLE | C189893 | Extended | JST
SM03B-GHS-TB(LF)(SN) | J8 | Connector_JST:JST_GH_SM03B-GHS-TB_1x03-1MP_P1.25mm_Horizontal | ~ | SM03B-GHS-TB(LF)(SN) | CONN 3 POS RIGHT ANGLE | C514175 | Extended | JST
4.7uH | L1 | Inductor_SMD:L_Bourns_SRP1038C_10.0x10.0mm | https://productfinder.pulseelectronics.com/api/open/part-attachments/datasheet/PA4342.472NLT | PA4342.472NLT | INDUCTOR 4.7uH 10A 15mΩ | C6949325 | Extended | Pulse Electronics
BSZ146N10LS5 | Q1,Q2,Q3 | Package_SON_JJ:Infineon_PG-TSDSON-8-26_3.3x3.3mm_P0.65mm_ThermalVias-D0.3mm | https://www.infineon.com/assets/row/public/documents/24/49/infineon-bsz146n10ls5-datasheet-en.pdf | BSZ146N10LS5ATMA1 | MOSFET N-CH 100V 44A TSDSON-8FL | C3289340 | Extended | Infineon Technologies
150k | R2 | Resistor_SMD:R_0603_1608Metric | ~ | 0603WAF1503T5E | RES 150kΩ 1% 75V 100mW 0603 | C22807 | Basic | UNI-ROYAL
12k | R3 | Resistor_SMD:R_0603_1608Metric | ~ | 0603WAF1202T5E | RES 12kΩ 1% 75V 100mW 0603 | C22790 | Basic | UNI-ROYAL
24k | R5 | Resistor_SMD:R_0603_1608Metric | ~ | 0603WAF2402T5E | RES 24kΩ 1% 75V 100mW 0603 | C23352 | Basic | UNI-ROYAL
560 | R10 | Resistor_SMD:R_0603_1608Metric | ~ | 0603WAF5600T5E | RES 560Ω 1% 75V 100mW 0603 | C23204 | Basic | UNI-ROYAL
10k | R13 | Resistor_SMD:R_0603_1608Metric | ~ | 0603WAF1002T5E | RES 10kΩ 1% 75V 100mW 0603 | C25804 | Basic | UNI-ROYAL
6.81k | R14 | Resistor_SMD:R_0603_1608Metric | ~ | RT0603BRD076K81L | RES 6.81kΩ 0.1% 50V 100mW 0603 | C861538 | Extended | YAGEO
3.48k | R15 | Resistor_SMD:R_0603_1608Metric | ~ | 0603WAD3481T5E | RES 3.48kΩ 0.5% 50V 100mW 0603 | C423043 | Extended | UNI-ROYAL
3.74k | R16 | Resistor_SMD:R_0603_1608Metric | https://www.yageogroup.com/products/Resistors/part/RT0603BRB073K74L | RT0603BRB073K74L | RES 3.74kΩ 0.1% 75V 100mW 0603 | C860375 | Extended | YAGEO
1k | R17 | Resistor_SMD:R_0805_2012Metric | ~ | 0805W8F1001T5E | RES 1kΩ 1% 150V 125mW 0805 | C17513 | Basic | UNI-ROYAL
1.5k | R1,R11 | Resistor_SMD:R_0603_1608Metric | ~ | 0603WAF1501T5E | RES 1.5kΩ 1% 75V 100mW 0603 | C22843 | Basic | UNI-ROYAL
2.2 | R4,R9 | Resistor_SMD:R_0603_1608Metric | ~ | 0603WAF220KT5E | RES 2.2Ω 1% 75V 100mW 0603 | C22939 | Basic | UNI-ROYAL
20k | R6,R8,R12 | Resistor_SMD:R_0603_1608Metric | ~ | 0603WAF2002T5E | RES 20kΩ 1% 75V 100mW 0603 | C4184 | Basic | UNI-ROYAL
LM5050-1 | U1 | Package_TO_SOT_SMD:TSOT-23-6 | http://www.ti.com/lit/ds/symlink/lm5050-1-q1.pdf | LM5050-1 | IC HIGH SIDE FET controller TSOT-23-6 | C473393 | Extended | Texas Instruments
LM5146 | U2 | Package_QFN_JJ:Texas_RGY0020B_EP_3.5x4.5mm_P0.5mm_ThermalVias-D0.3mm | https://www.ti.com/lit/gpn/lm5146 | LM5146RGYR | IC BUCK SYNC Controller VQFN-20 | C3188679 | Extended | Texas Instruments

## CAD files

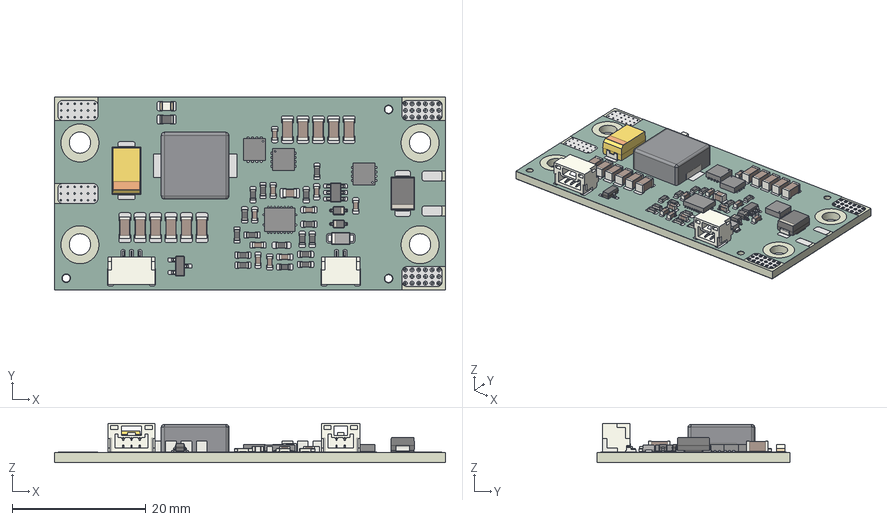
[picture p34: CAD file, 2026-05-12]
kicad/SSDV3.step
58.4 x 28.8 x 5.88 mm
C_1206_3216Metric x 11
D_SOD-323 x 2
C_0603_1608Metric x 10
R_0603_1608Metric x 16
JST_GH_SM03B-GHS-TB_1x03-1MP_P1.25mm_Horizontal
ISZ15EP15LMATMA1_ISZ15EP15LMATMA1 x 3
C_0805_2012Metric
TSOT-23-6
CP_EIA-7343-31_Kemet-D
D_SMB
L_Bourns_SRP1050WA
LED_0805_2012Metric
JST_GH_SM02B-GHS-TB_1x02-1MP_P1.25mm_Horizontal
SOT-23-3
R_0805_2012Metric
BODY-QFN_AF0
PIN1-ID
D_SMF
SSDV3_pad
SSDV3_soldermask
SSDV3_PCB

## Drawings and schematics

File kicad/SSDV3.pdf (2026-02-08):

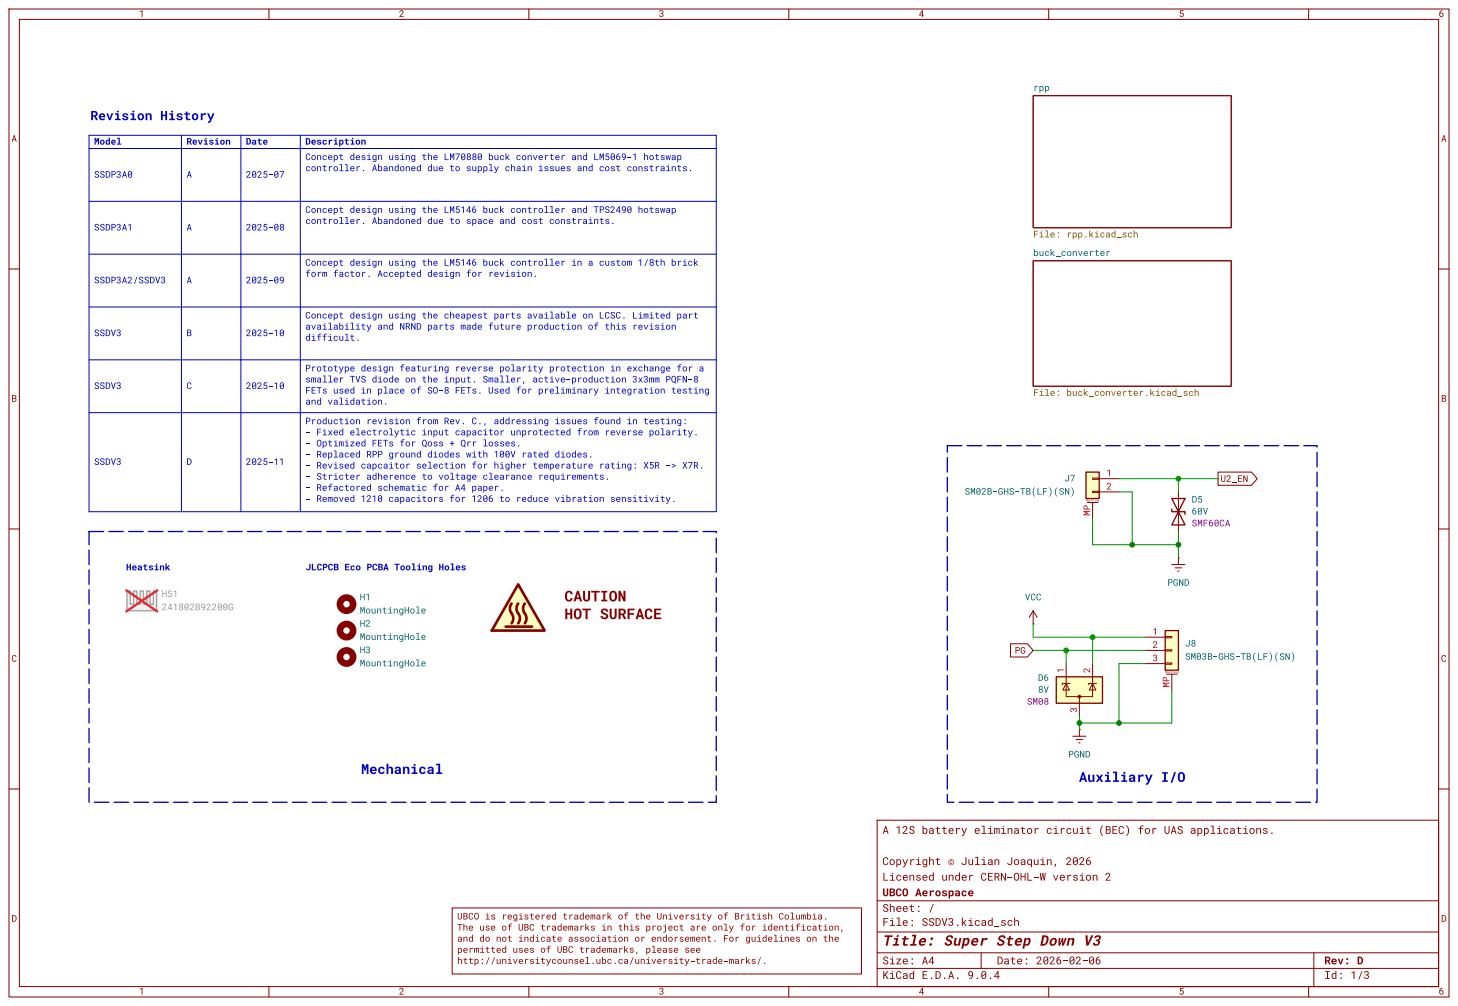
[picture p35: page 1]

A | 2025-08 | controller. Concept design using the LM5146 buck controller Abandoned due to supply chain issues and cost constraints. SSDP3A1 and TPS2490 hotswap

A | 2025-09 | controller. Concept design using the LM5146 buck controller Abandoned due to space and cost constraints. SSDP3A2/SSDV3 in a custom 1/8th brick

B | 2025-10 | form factor. Concept design using the cheapest parts available Accepted design for revision. SSDV3 and NRNDparts made future production on LCSC. Limited of this revision part availability

C | 2025-10 | difficult. SSDV3 Prototype design featuring reverse polarity protection in exchange for a

smaller TVS diode on the input. Smaller, active-production integration 3x3mm PQFN-8 FETs used in place of SO-8 FETs. Used for preliminary testing

J7 SM02B-GHS-TB(LF)(SN) 3

J8SM03B-GHS-TB(LF)(SN) PGND

http://universitycounsel.ubc.ca/university-trade-marks/.

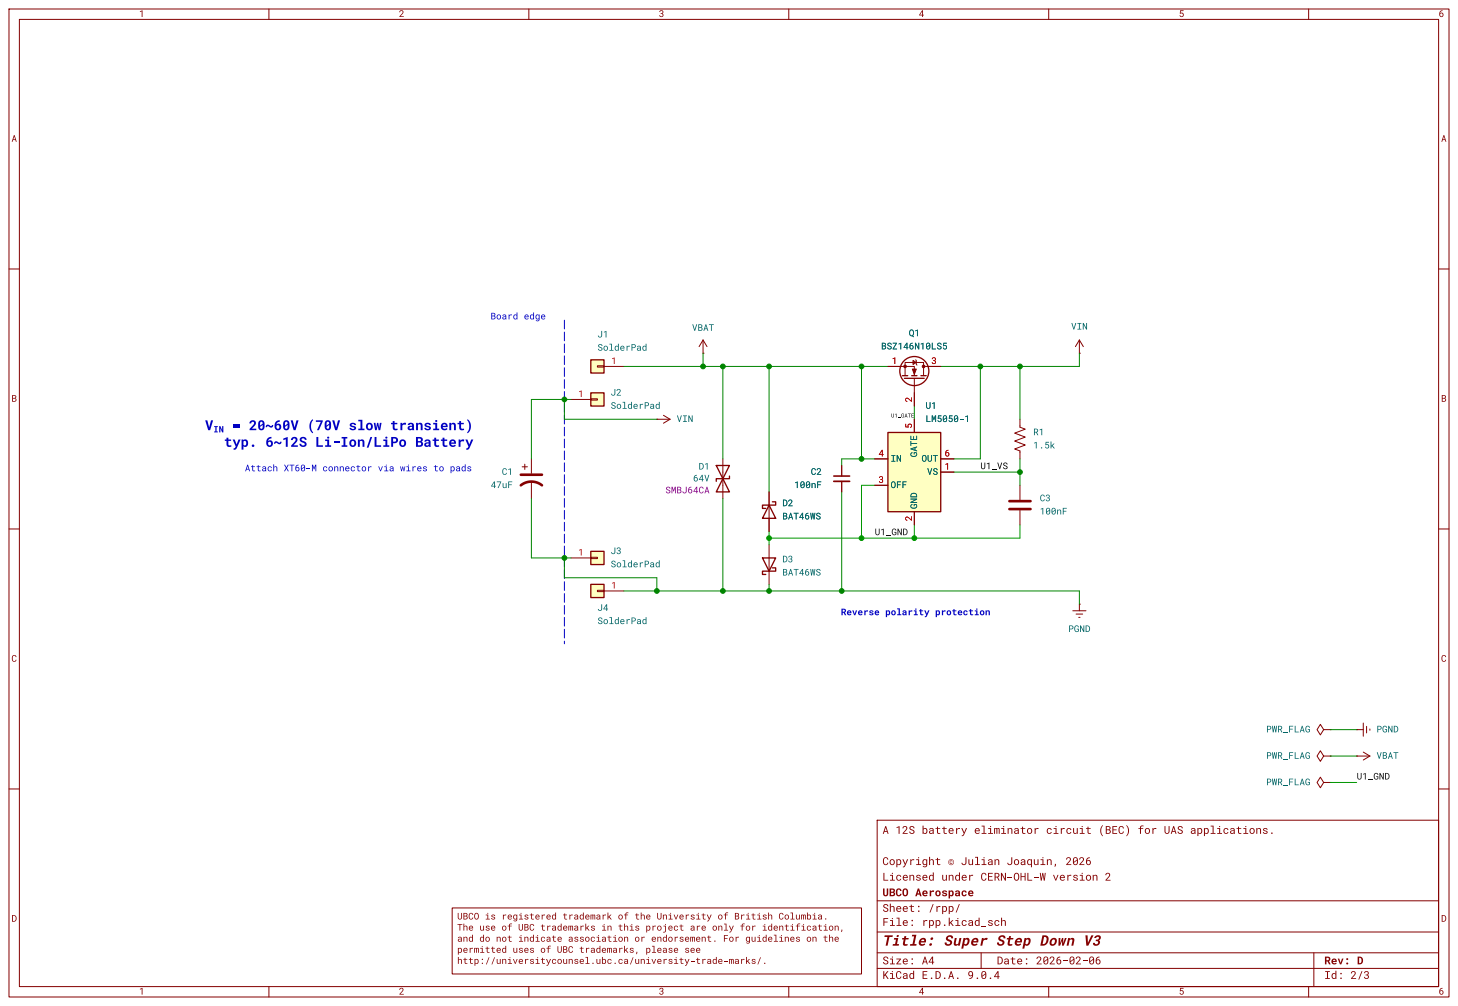
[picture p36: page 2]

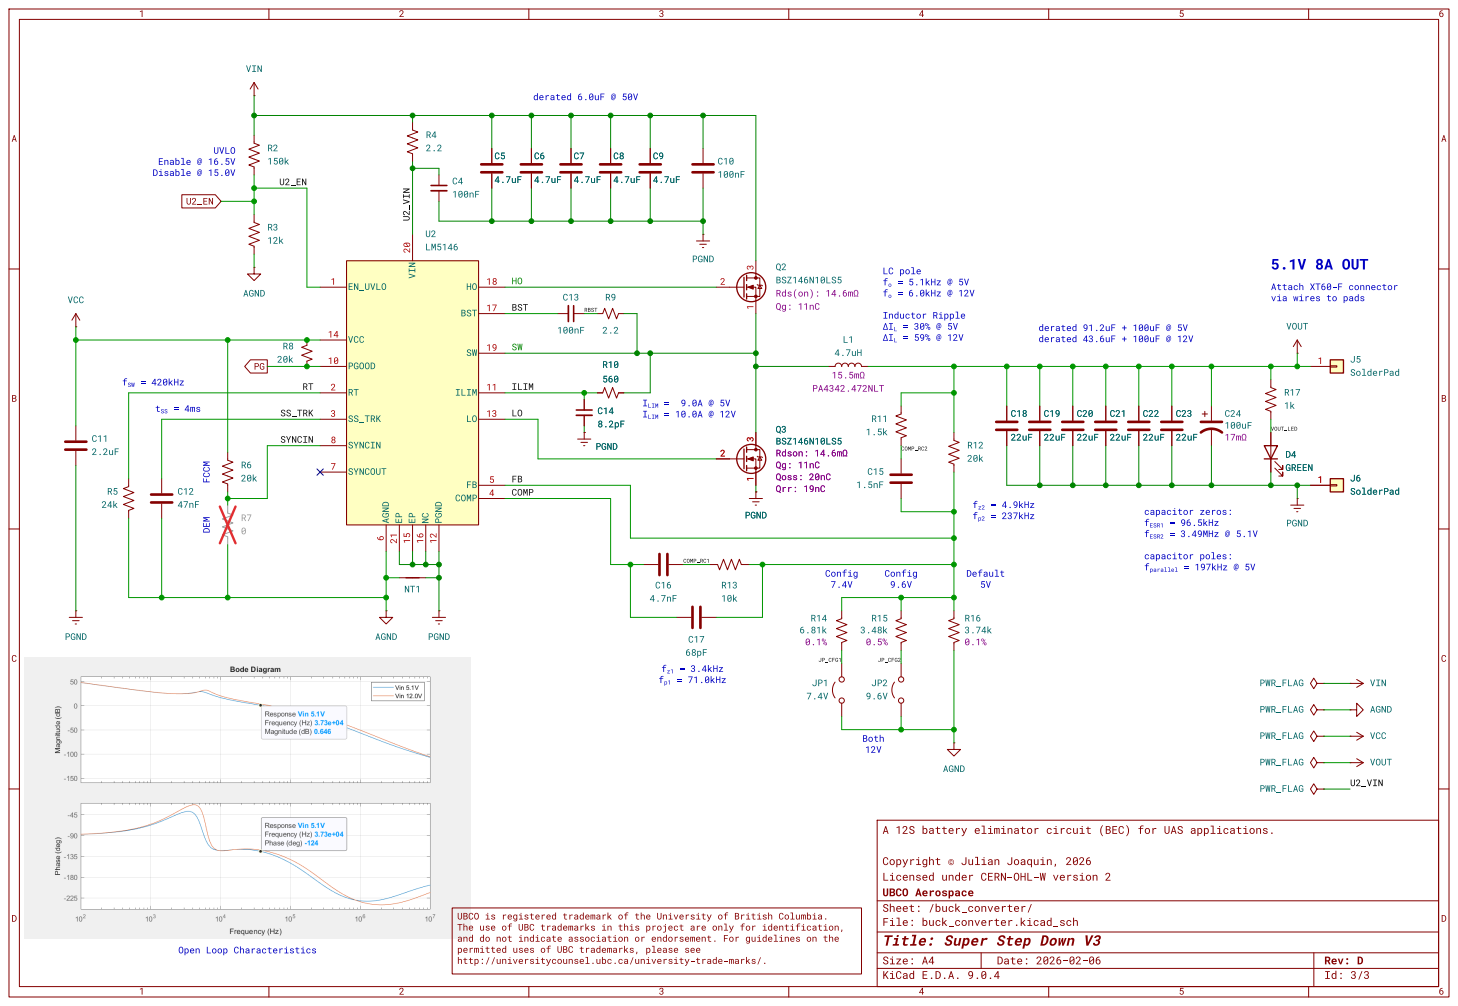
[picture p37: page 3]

6 EP 21 VIN 20 EP 15 NC 16 PGND 12 HO

LC pole
f_{o}= 5.1kHz @ 5V
Attach XT60-F connector via wires to pads Both
f_{o}= 6.0kHz @ 12V

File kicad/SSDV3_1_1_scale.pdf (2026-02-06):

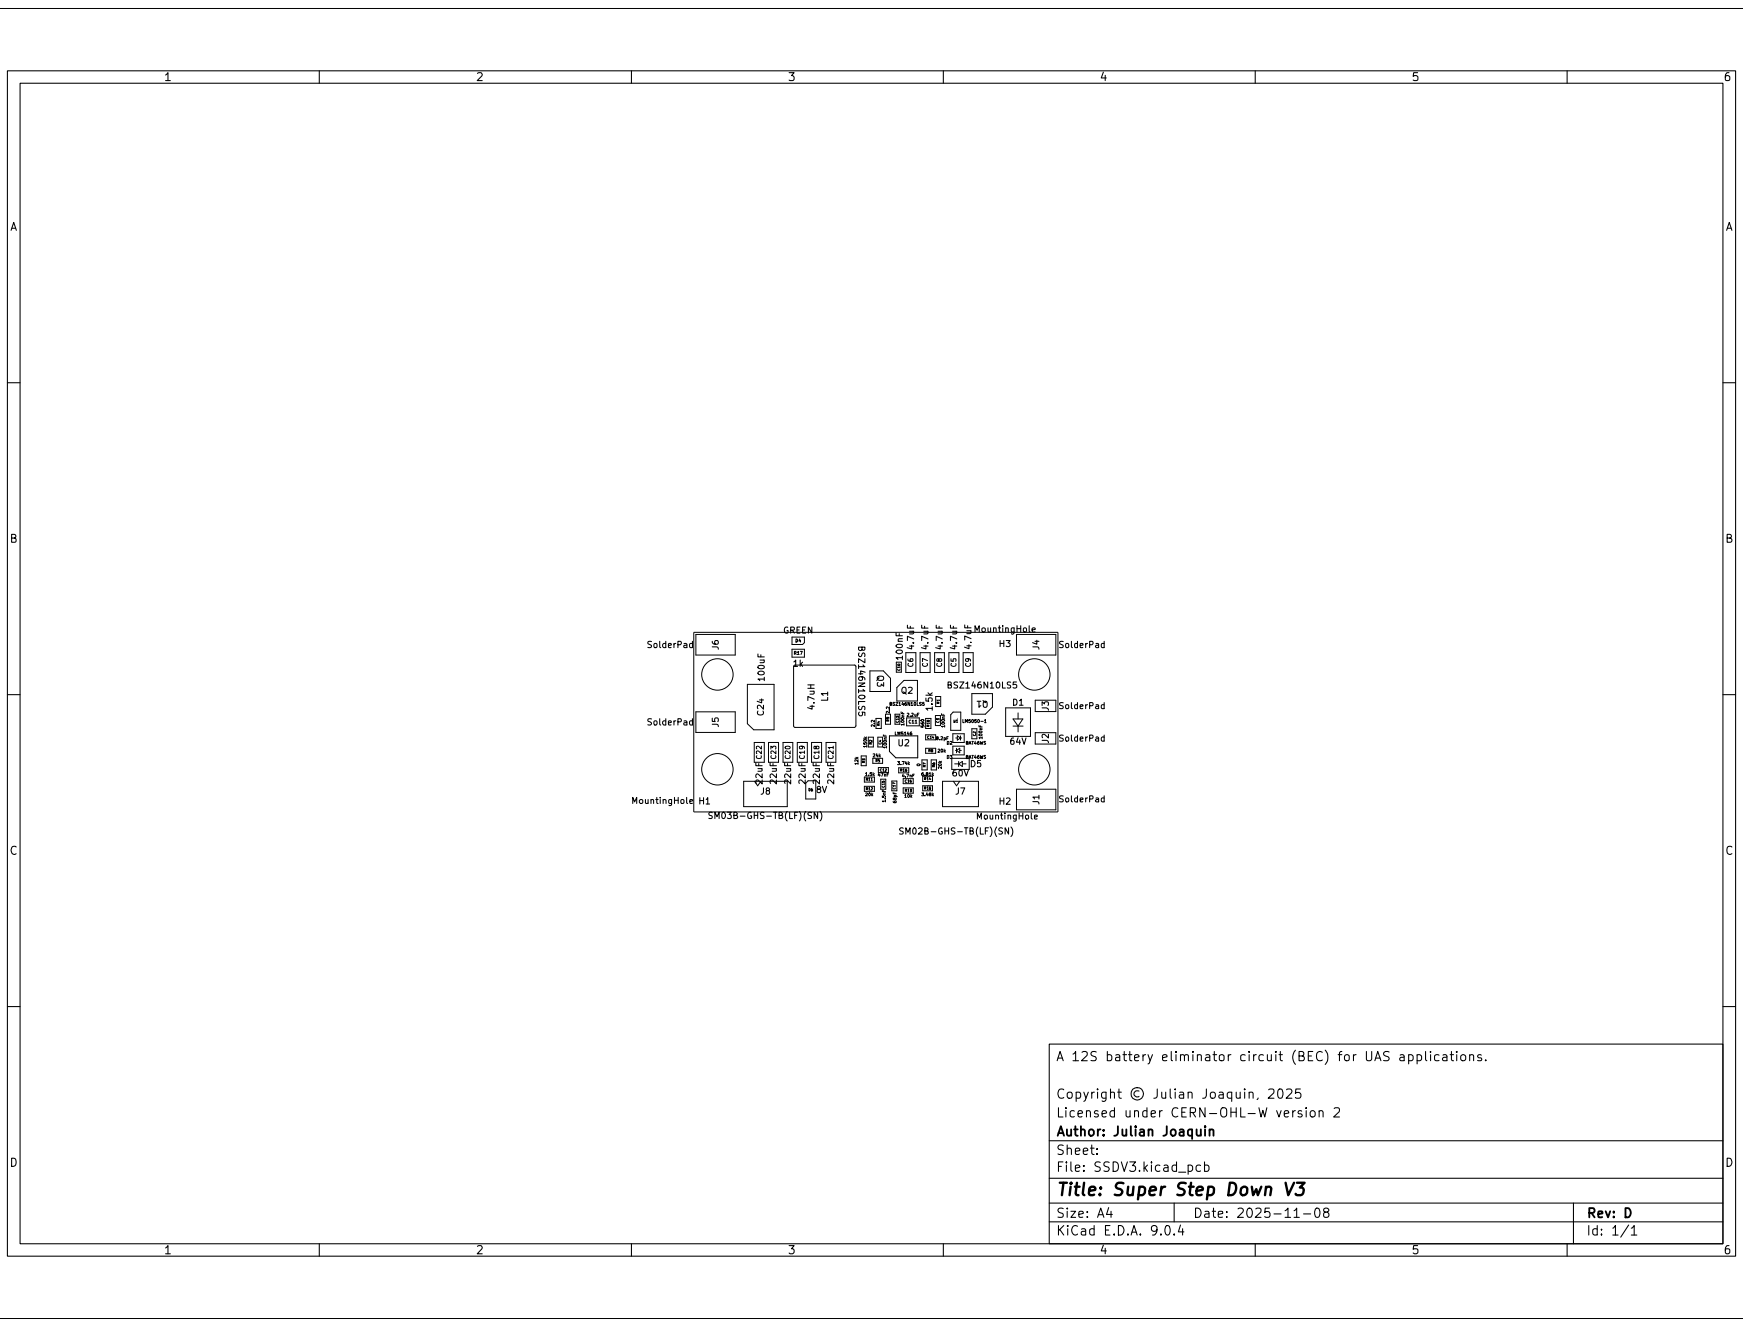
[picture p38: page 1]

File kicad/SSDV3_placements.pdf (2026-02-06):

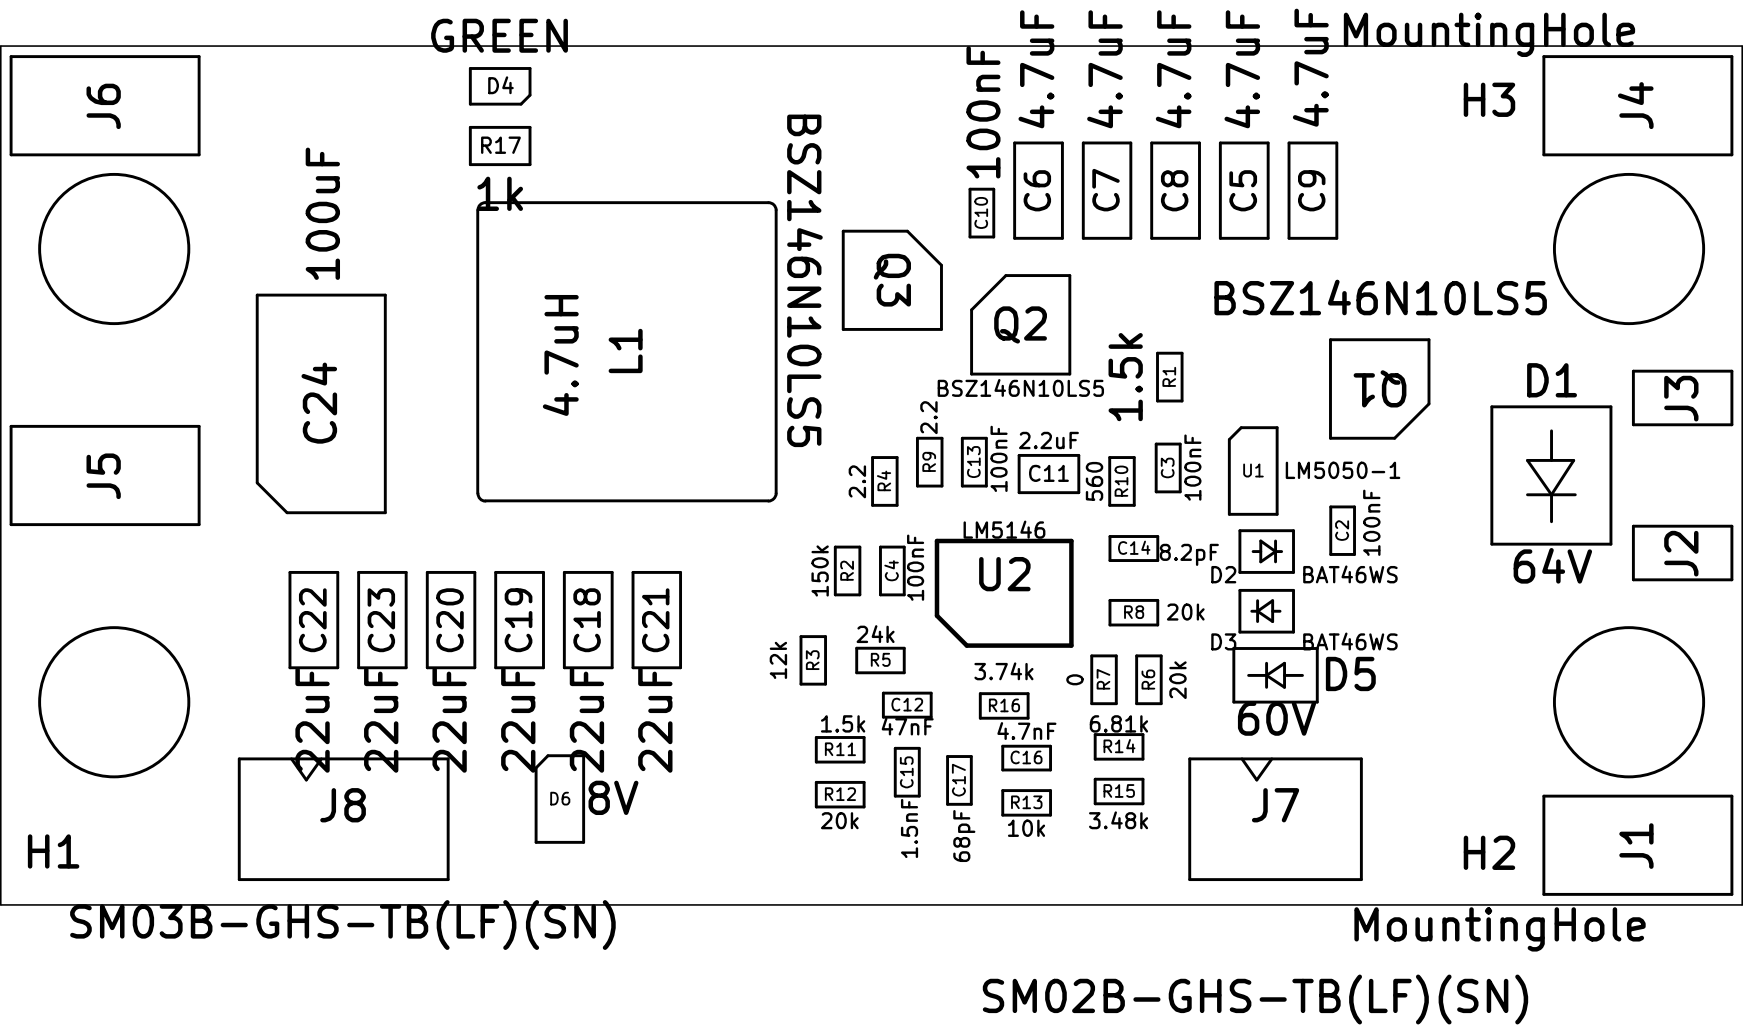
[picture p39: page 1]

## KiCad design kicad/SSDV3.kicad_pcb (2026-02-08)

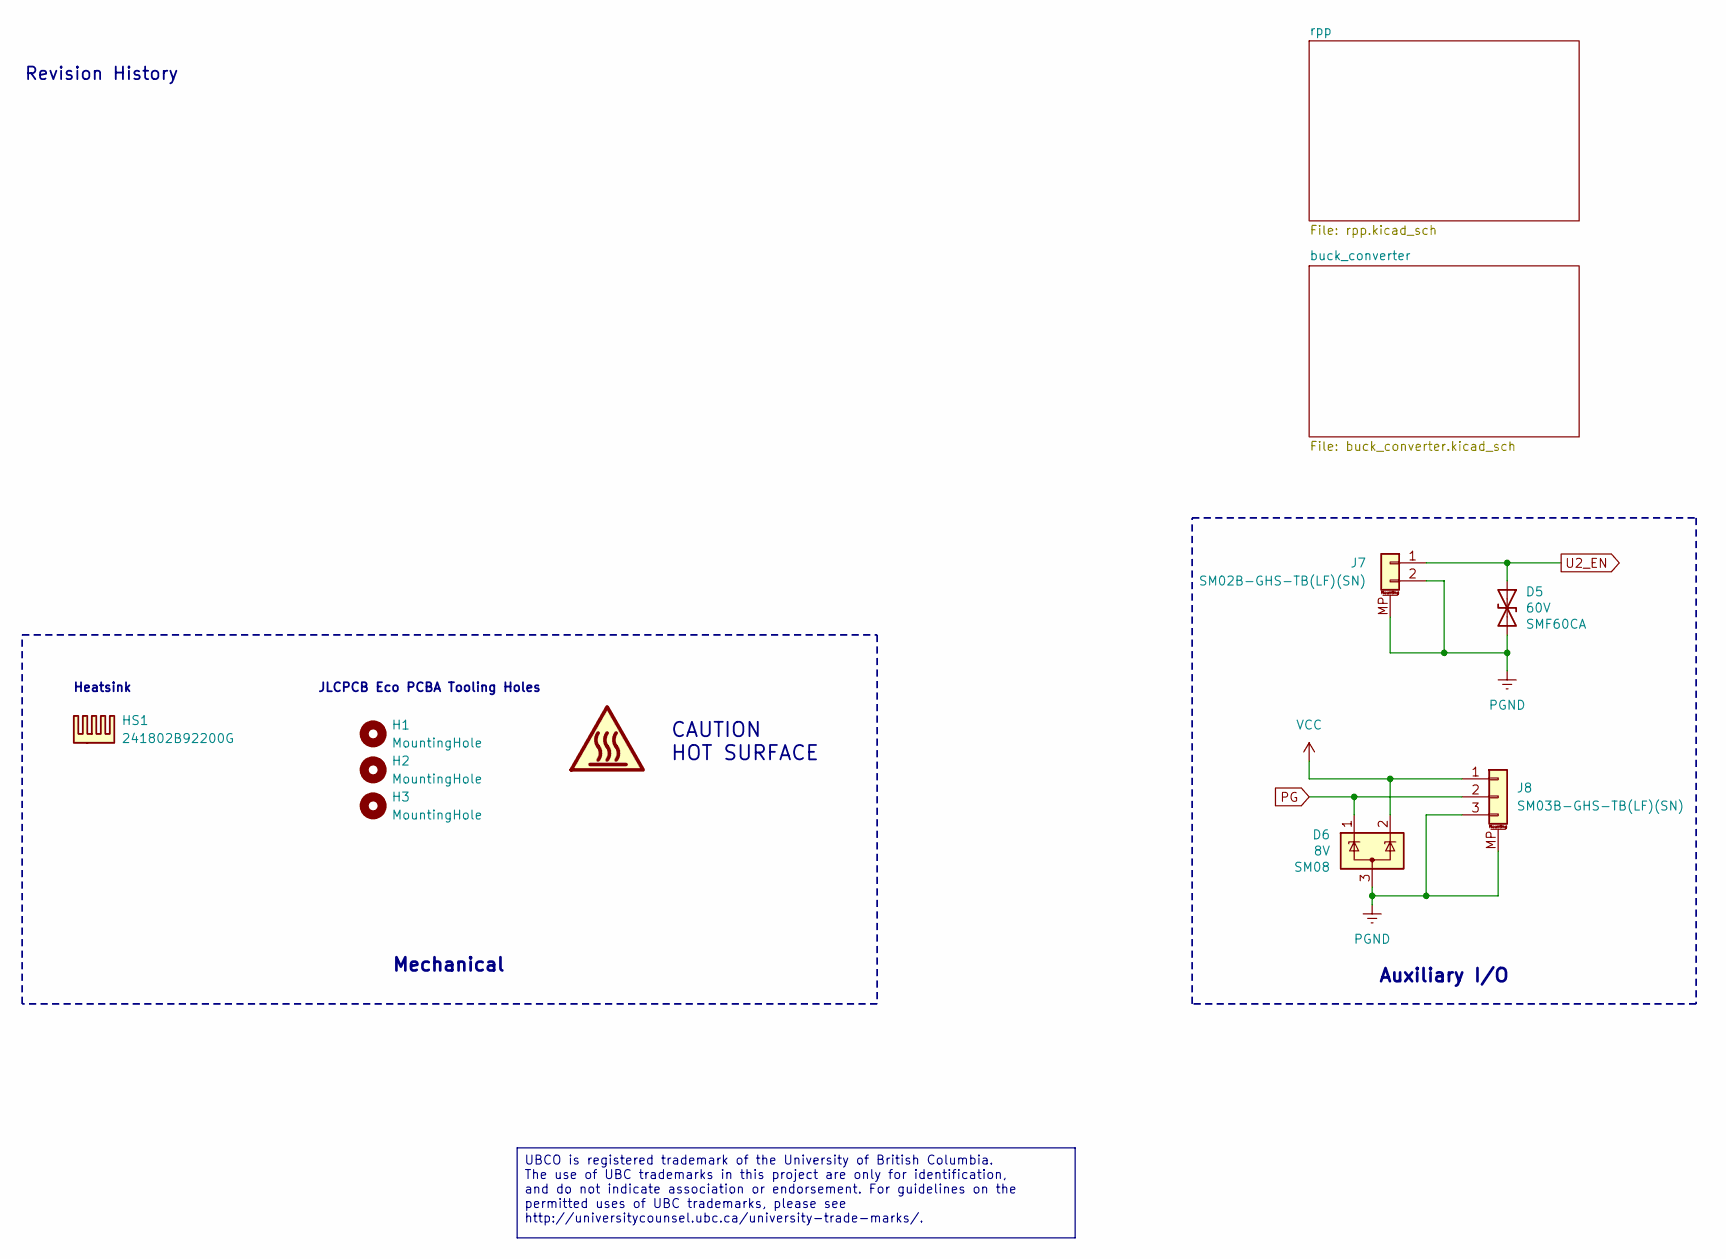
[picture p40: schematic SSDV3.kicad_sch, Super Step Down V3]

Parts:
D5: 60V; D_SMF; Voltage 60V; Part Number SMF60CA; LCSC PN C41376092
D6: 8V; SOT-23-3; Voltage 8V; Part Number SM08; LCSC PN C42413902
H1, H2, H3: MountingHole; ToolingHole_1.152mm
HS1: 241802B92200G; 24180xB9x200G
J7: SM02B-GHS-TB(LF)(SN); JST_GH_SM02B-GHS-TB_1x02-1MP_P1.25mm_Horizontal; Part Number SM02B-GHS-TB(LF)(SN); LCSC PN C189893
J8: SM03B-GHS-TB(LF)(SN); JST_GH_SM03B-GHS-TB_1x03-1MP_P1.25mm_Horizontal; Part Number SM03B-GHS-TB(LF)(SN); LCSC PN C514175

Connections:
PG: D6.1 (K), J8.2; also elsewhere on the board
PGND: D5.2 (A2), D6.3 (A), J7.2, J7.MP (MountPin), J8.3, J8.MP (MountPin); also elsewhere on the board
U2_EN: D5.1 (A1), J7.1; also elsewhere on the board
VCC: D6.2 (K), J8.1; also elsewhere on the board

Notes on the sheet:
Heatsink
Auxiliary I/O
CAUTION HOT SURFACE
Revision History
JLCPCB Eco PCBA Tooling Holes
Mechanical
UBCO is registered trademark of the University of British Columbia. The use of UBC trademarks in this project are only for identification, and do not indicate association or endorsement. For guidelines on the permitted uses of UBC trademarks, please see http://universitycounsel.ubc.ca/university-tr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

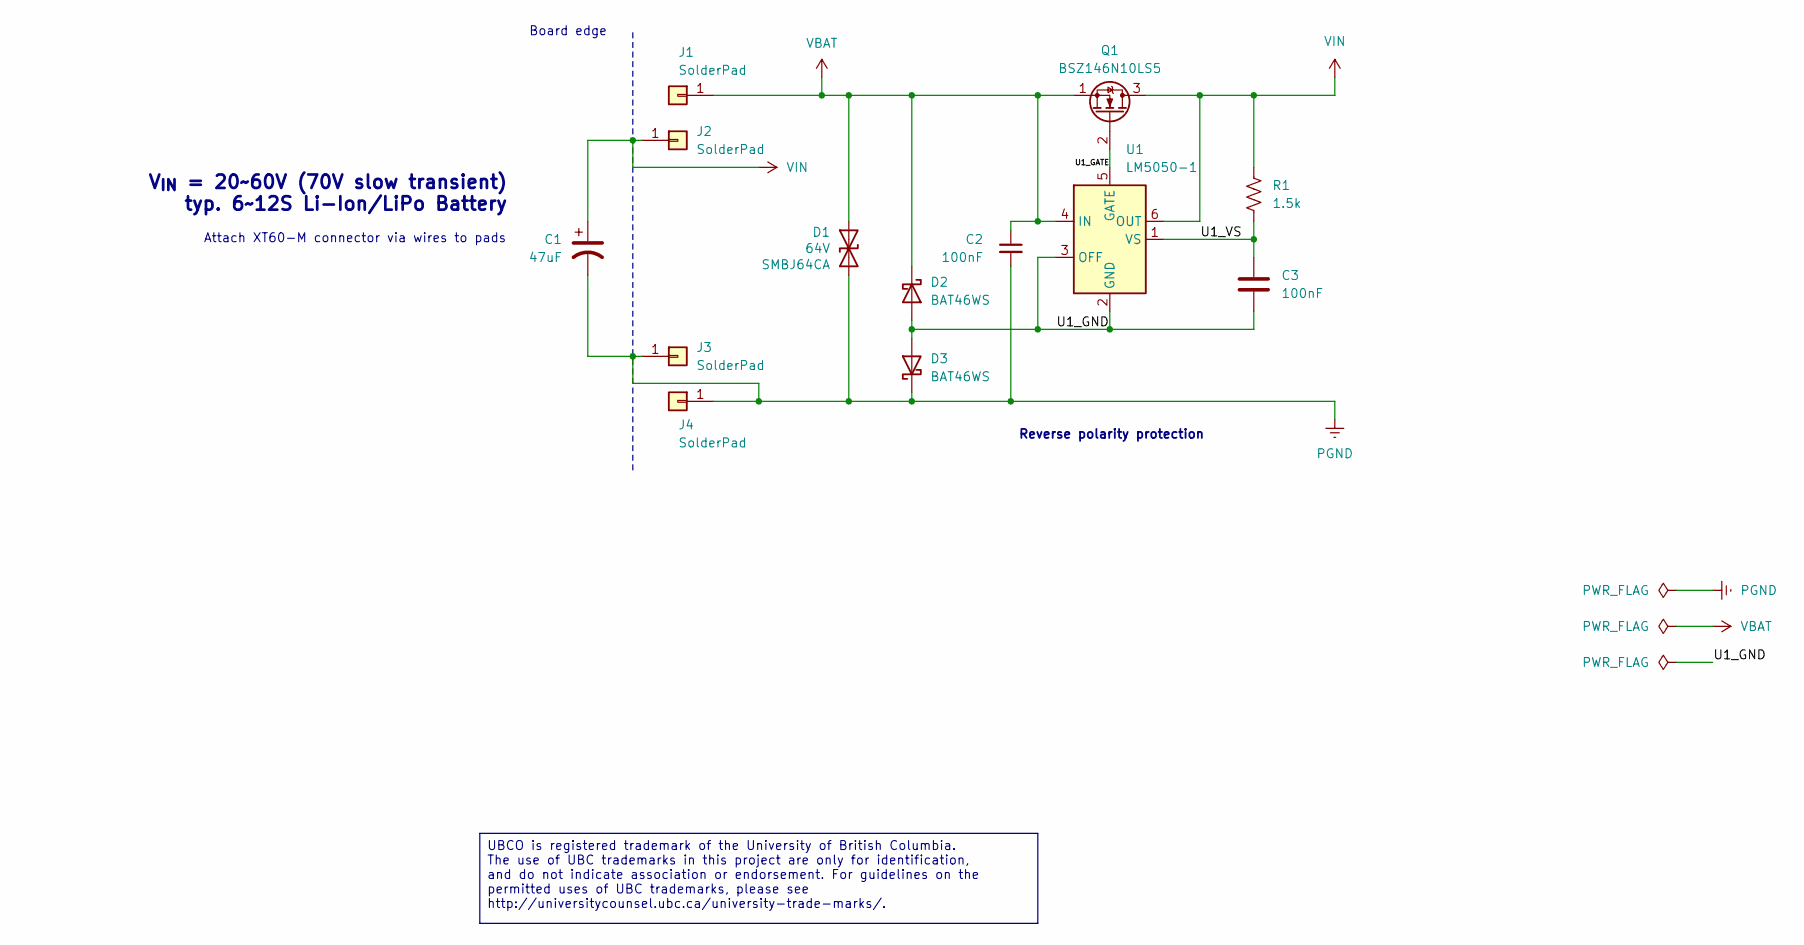
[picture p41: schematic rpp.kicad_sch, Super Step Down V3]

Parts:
C1: 47uF; Part Number ESH476M100AH9AA; LCSC PN C5113349
C2, C3: 100nF; C_0603_1608Metric; Voltage 100V; Tolerance 10%; Part Type Extended; LCSC PN C113803
D1: 64V; D_SMB; Voltage 103V; Part Number SMBJ64CA; LCSC PN C41376099
D2, D3: BAT46WS; D_SOD-323; Part Number BAT46WS; LCSC PN C7502692
J1, J4: SolderPad; SolderWirePad_1x01_SMD_3x6mm
J2, J3: SolderPad; SolderWirePad_1x01_SMD_1.5x3mm
Q1: BSZ146N10LS5; Infineon_PG-TSDSON-8-26_3.3x3.3mm_P0.65mm_ThermalVias-D0.3mm; Part Number BSZ146N10LS5ATMA1; LCSC PN C3289340
R1: 1.5k; R_0603_1608Metric; Voltage 75V; Tolerance 1%; Part Type Basic; LCSC PN C22843
U1: LM5050-1; TSOT-23-6; Part Number LM5050-1; LCSC PN C473393

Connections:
/rpp/U1_GATE: Q1.2 (G), U1.5 (GATE)
/rpp/U1_GND: C3.2, D2.2 (A), D3.2 (A), U1.2 (GND), U1.3 (OFF)
/rpp/U1_VS: C3.1, R1.2, U1.1 (VS)
PGND: C1.2, C2.2, D1.2 (A2), D3.1 (K), J3.1, J4.1; also elsewhere on the board
VBAT: C2.1, D1.1 (A1), D2.1 (K), J1.1, Q1.1 (S), U1.4 (IN)
VIN: C1.1, J2.1, Q1.3 (D), R1.1, U1.6 (OUT); also elsewhere on the board

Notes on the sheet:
Reverse polarity protection
Board edge
V_{IN} = 20~60V (70V slow transient) typ. 6~12S Li-Ion/LiPo Battery
Attach XT60-M connector via wires to pads
UBCO is registered trademark of the University of British Columbia. The use of UBC trademarks in this project are only for identification, and do not indicate association or endorsement. For guidelines on the permitted uses of UBC trademarks, please see http://universitycounsel.ubc.ca/university-tr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

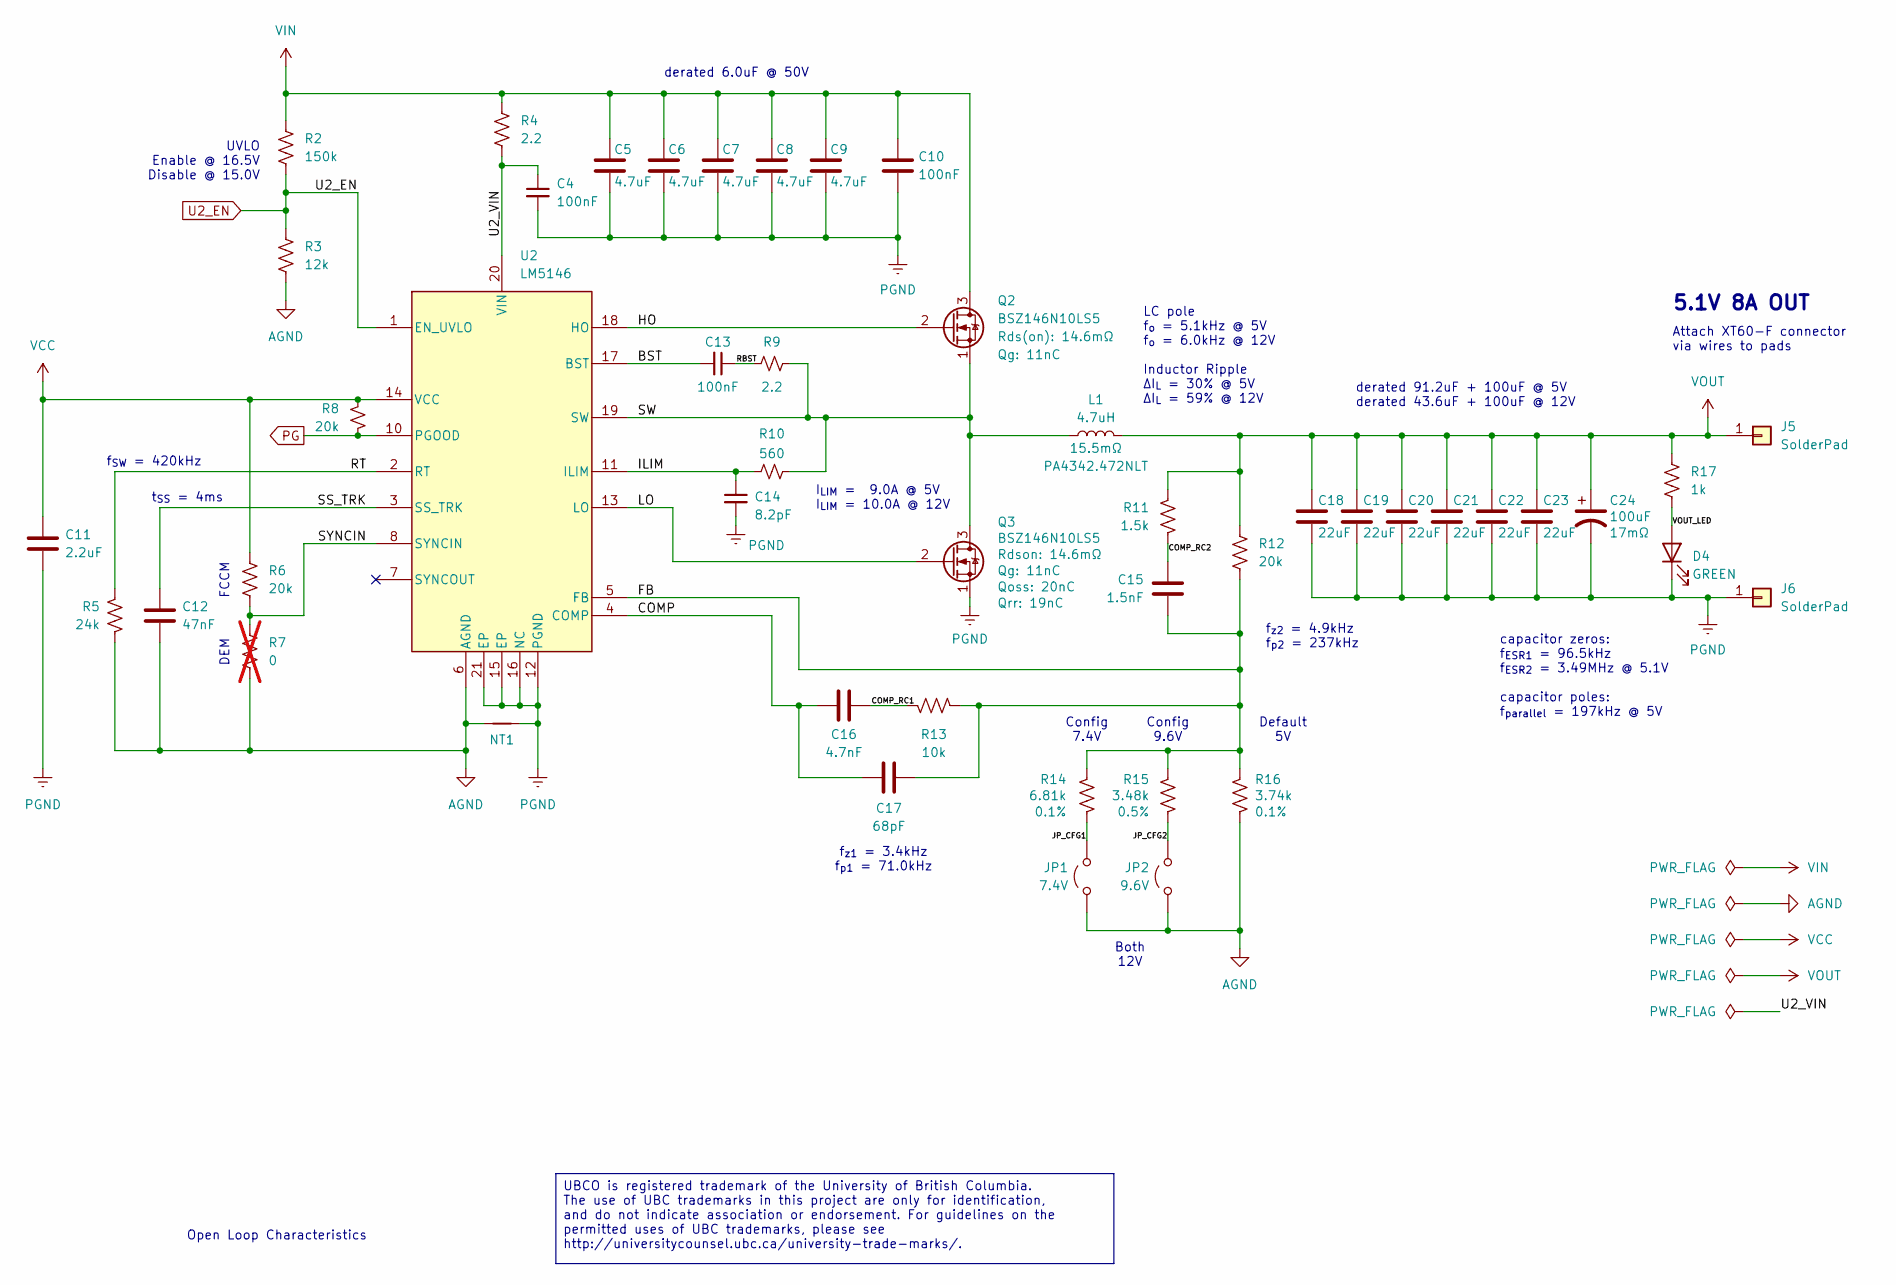
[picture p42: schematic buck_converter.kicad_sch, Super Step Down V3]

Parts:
C4, C10, C13: 100nF; C_0603_1608Metric; Voltage 100V; Tolerance 10%; Part Type Extended; LCSC PN C113803
C5, C6, C7, C8, C9: 4.7uF; C_1206_3216Metric; Voltage 100V; Tolerance 10%; Part Type Extended; LCSC PN C3864744
C11: 2.2uF; C_0805_2012Metric; Voltage 25V; Tolerance 10%; Part Type Extended; LCSC PN C77081
C12: 47nF; C_0603_1608Metric; Voltage 50V; Tolerance 10%; Part Type Basic; LCSC PN C1622
C14: 8.2pF; C_0603_1608Metric; Voltage 100V; Tolerance 5%; Part Type Extended; LCSC PN C2212506
C15: 1.5nF; C_0603_1608Metric; Voltage 50V; Tolerance 10%; Part Type Preferred Extended; LCSC PN C1595
C16: 4.7nF; C_0603_1608Metric; Voltage 50V; Tolerance 10%; Part Type Basic; LCSC PN C53987
C17: 68pF; C_0603_1608Metric; Voltage 50V; Tolerance 5%; Part Type Preferred Extended; LCSC PN C28262
C18, C19, C20, C21, C22, C23: 22uF; C_1206_3216Metric_Pad1.33x1.80mm_HandSolder; Voltage 25V; Tolerance 10%; Part Type Extended; LCSC PN C5272872
C24: 100uF; CP_EIA-7343-20_Kemet-V_HandSolder; Tolerance 20%; Voltage 25V; Part Type Extended; LCSC PN C212710
D4: GREEN; LED_0805_2012Metric; Part Type Basic; LCSC PN C2297
J5, J6: SolderPad; SolderWirePad_1x01_SMD_3x6mm
JP1: 7.4V; SolderJumper-2_P1.3mm_Open_TrianglePad1.0x1.5mm
JP2: 9.6V; SolderJumper-2_P1.3mm_Open_TrianglePad1.0x1.5mm
L1: 4.7uH; L_Bourns_SRP1038C_10.0x10.0mm; Tolerance 20%; Part Number PA4342.472NLT; LCSC PN C6949325
NT1: NetTie_2; NetTie-2_SMD_Pad0.5mm
Q2: BSZ146N10LS5; Infineon_PG-TSDSON-8-26_3.3x3.3mm_P0.65mm_ThermalVias-D0.3mm; Voltage 100V; Part Type Extended; LCSC PN C3289340
Q3: BSZ146N10LS5; Infineon_PG-TSDSON-8-26_3.3x3.3mm_P0.65mm_ThermalVias-D0.3mm; Voltage 100V; Part Number BSZ146N10LS5ATMA1; LCSC PN C3289340
R2: 150k; R_0603_1608Metric; Tolerance 1%; Voltage 75V; Part Type Basic; LCSC PN C22807
R3: 12k; R_0603_1608Metric; Tolerance 1%; Voltage 75V; Part Type Basic; LCSC PN C22790
R4, R9: 2.2; R_0603_1608Metric; Voltage 75V; Tolerance 1%; Part Type Basic; LCSC PN C22939
R5: 24k; R_0603_1608Metric; Voltage 75V; Tolerance 1%; Part Type Basic; LCSC PN C23352
R6, R8, R12: 20k; R_0603_1608Metric; Voltage 75V; Tolerance 1%; Part Type Basic; LCSC PN C4184
R7: 0; R_0603_1608Metric; not fitted
R10: 560; R_0603_1608Metric; Voltage 75V; Tolerance 1%; Part Type Basic; LCSC PN C23204
R11: 1.5k; R_0603_1608Metric; Voltage 75V; Tolerance 1%; Part Type Basic; LCSC PN C22843
R13: 10k; R_0603_1608Metric; Voltage 75V; Tolerance 1%; Part Type Basic; LCSC PN C25804
R14: 6.81k; R_0603_1608Metric; Voltage 50V; Tolerance 0.1%; Part Type Extended; LCSC PN C861538
R15: 3.48k; R_0603_1608Metric; Voltage 50V; Tolerance 0.5%; Part Type Extended; LCSC PN C423043
R16: 3.74k; R_0603_1608Metric_Pad0.98x0.95mm_HandSolder; Tolerance 0.1%; Voltage 75V; Part Type Extended; LCSC PN C860375
R17: 1k; R_0805_2012Metric; Voltage 150V; Tolerance 1%; Part Type Basic; LCSC PN C17513
U2: LM5146; Texas_RGY0020B_EP_3.5x4.5mm_P0.5mm_ThermalVias-D0.3mm; Voltage 100V; Part Type Extended; LCSC PN C3188679

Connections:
/buck_converter/BST: C13.2, U2.17 (BST)
/buck_converter/COMP: C16.1, C17.2, U2.4 (COMP)
/buck_converter/COMP_RC1: C16.2, R13.2
/buck_converter/COMP_RC2: C15.1, R11.2
/buck_converter/FB: C15.2, C17.1, R12.2, R13.1, R14.1, R15.1, R16.1, U2.5 (FB)
/buck_converter/HO: Q2.2 (G), U2.18 (HO)
/buck_converter/ILIM: C14.1, R10.2, U2.11 (ILIM)
/buck_converter/JP_CFG1: JP1.2 (B), R14.2
/buck_converter/JP_CFG2: JP2.2 (B), R15.2
/buck_converter/LO: Q3.2 (G), U2.13 (LO)
/buck_converter/RBST: C13.1, R9.1
/buck_converter/RT: R5.1, U2.2 (RT)
/buck_converter/SS_TRK: C12.1, U2.3 (SS_TRK)
/buck_converter/SW: L1.1, Q2.1 (S), Q3.3 (D), R9.2, R10.1, U2.19 (SW)
/buck_converter/SYNCIN: R6.2, R7.1, U2.8 (SYNCIN)
/buck_converter/U2_VIN: C4.1, R4.2, U2.20 (VIN)
/buck_converter/VOUT_LED: D4.2 (A), R17.2
AGND: C12.2, JP1.1 (A), JP2.1 (A), NT1.2, R3.2, R5.2, R7.2, R16.2, U2.6 (AGND)
PG: R8.2, U2.10 (PGOOD); also elsewhere on the board
PGND: C4.2, C5.2, C6.2, C7.2, C8.2, C9.2, C10.2, C11.2, C14.2, C18.2, C19.2, C20.2, C21.2, C22.2, C23.2, C24.2, D4.1 (K), J6.1, NT1.1, Q3.1 (S), U2.12 (PGND), U2.15 (EP), U2.16 (NC), U2.21 (EP); also elsewhere on the board
U2_EN: R2.2, R3.1, U2.1 (EN_UVLO); also elsewhere on the board
VCC: C11.1, R6.1, R8.1, U2.14 (VCC); also elsewhere on the board
VIN: C5.1, C6.1, C7.1, C8.1, C9.1, C10.1, Q2.3 (D), R2.1, R4.1; also elsewhere on the board
VOUT: C18.1, C19.1, C20.1, C21.1, C22.1, C23.1, C24.1, J5.1, L1.2, R11.1, R12.1, R17.1

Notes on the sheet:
capacitor zeros: f_{ESR1} = 96.5kHz f_{ESR2} = 3.49MHz @ 5.1V capacitor poles: f_{parallel} = 197kHz @ 5V
f_{SW} = 420kHz
FCCM
t_{SS} = 4ms
Config 9.6V
Open Loop Characteristics
DEM
Default 5V
5.1V 8A OUT
derated 6.0uF @ 50V
UVLO Enable @ 16.5V Disable @ 15.0V
Config 7.4V
Attach XT60-F connector via wires to pads
f_{z1} = 3.4kHz f_{p1} = 71.0kHz
f_{z2} = 4.9kHz f_{p2} = 237kHz
I_{LIM} = 9.0A @ 5V I_{LIM} = 10.0A @ 12V
Both 12V
LC pole f_{o} = 5.1kHz @ 5V f_{o} = 6.0kHz @ 12V Inductor Ripple ΔI_{L} = 30% @ 5V ΔI_{L} = 59% @ 12V
derated 91.2uF + 100uF @ 5V derated 43.6uF + 100uF @ 12V
UBCO is registered trademark of the University of British Columbia. The use of UBC trademarks in this project are only for identification, and do not indicate association or endorsement. For guidelines on the permitted uses of UBC trademarks, please see http://universitycounsel.ubc.ca/university-tr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

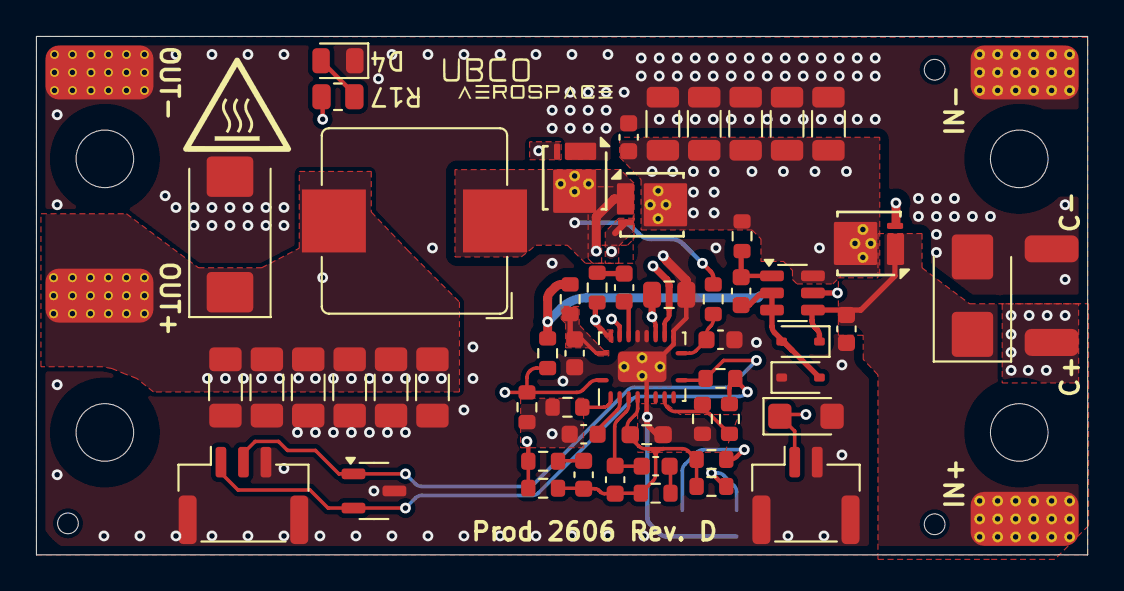
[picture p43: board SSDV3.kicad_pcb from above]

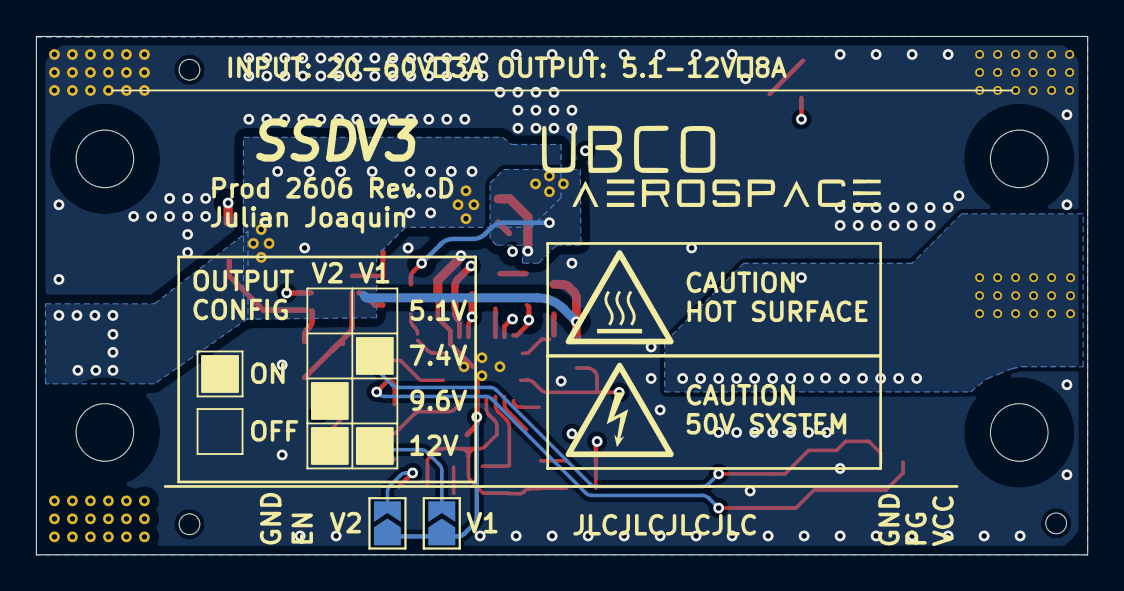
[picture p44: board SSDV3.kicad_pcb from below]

Board: 4 copper layers, 58.4 x 28.8 mm, 67 parts (3 on the bottom side), 28 nets.

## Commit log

2025-11-09 Adjusted licensing for club
    [SSDV3.kicad_pcb, SSDV3.kicad_sch, buck_converter.kicad_sch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]
2025-11-23 Added heatsink footprint
    [SSDV3.kicad_pcb, SSDV3.kicad_sch, rpp.kicad_sch]
2025-12-02 Addressed HS FET failure mode from revC
    [SSDV3.kicad_pcb, buck_converter.kicad_sch]
2025-12-17 Created redesign for revD to reduce thermal stress
    [SSDV3.kicad_pcb, SSDV3.kicad_sch, buck_converter.kicad_sch]
2026-02-02 FET Optimizations
    [SSDV3-cygnus.kicad_sch, SSDV3.kicad_pcb, buck_converter.kicad_sch]
2026-02-06 RevD finished
    [SSDV3-cygnus.kicad_sch, SSDV3.csv]
2026-02-06 Wrong design files initially commited
    [SSDV3.kicad_pcb, SSDV3.kicad_sch, buck_converter.kicad_sch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]
2026-02-07 Added UBCO trademark notice, prepared for production
    [SSDV3.kicad_pcb, SSDV3.kicad_sch, buck_converter.kicad_sch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]
2026-02-07 Final production files
    [SSDV3.kicad_pcb, SSDV3.kicad_sch, buck_converter.kicad_sch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]
2026-02-07 Component optimizations
    [SSDV3.kicad_pcb, SSDV3.kicad_sch, buck_converter.kicad_sch]
2026-02-08 Minor technical corrections
    [SSDV3.kicad_pcb, SSDV3.kicad_sch, buck_converter.kicad_sch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]
2026-05-12 Rev D production photos and 3D render
    [SSDV3.step]
2026-05-17 RevE New symbols and footprints
